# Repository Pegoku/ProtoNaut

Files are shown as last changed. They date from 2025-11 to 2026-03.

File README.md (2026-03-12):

# ProtoNaut

ProtoNaut is a custom-designed 3D printer. Built using 2020 aluminum extrusions, linear rails, and NEMA 17 stepper motors, this printer aims to deliver reliable performance in a compact cantilever design while maintaining a budget-ish build cost of approximately $400.

The project utilizes Klipper for motion control, running on an Orange Pi Zero 3 with a BIGTREETECH SKR PICO controller. The design tries to achieve precision, ease of assembly, and fully open-source design through FreeCAD CAD files.

## Images

BUILD

<details>
<summary>CAD - click to expand</summary>

ProtoNaut CAD

</details>

## Features

- Cantilever Design
- Magnetic PEI Bed
- Automatic Bed Leveling using the BTT EDDY  
- Klipper firmware
- 150x150mm Build Volume

## BOM (Bill of Materials)
[ONLINE GOOGLE SHEETS](https://docs.google.com/spreadsheets/d/10S4NtRr_S8fiZ1eurKxR3v34cEba0Mtye6buwyMkIno/edit?usp=sharing)

| Item | Qtty | 4.19€  | Source | Extra | Category | Item Total | Final Total | Final Total ($) |
| --- | ---- | --- | --- | --- | --- | --- | --- | --- |
| Bed Spring Leveling kit | 1 | 5.19€  | https://es.aliexpress.com/item/1005003097384079.html  | Black(M3) 1Set | Bed | 5.19€ | 346.64€ | $398.13 |
| Bed support Y axis | 1 | 10.49€ | https://es.aliexpress.com/item/1005005526138056.html  | | Bed | 10.49€ | | |
| 12V 80W heatbed 150x150 | 1 | 8.59€  | https://es.aliexpress.com/item/1005001417127602.html  | | Bed | 8.59€ | | |
| Magnetic Sticker | 1 | 5.09€  | https://es.aliexpress.com/item/1005007297499038.html  | | Bed | 5.09€ | | |
| Orange Pi Zero 3 | 1 | 21.11€ | https://es.aliexpress.com/item/1005005785695181.html  | Bundle 3, 1GB RAM | Electronics | 21.11€ | | |
| BIGTREETECH SKR PICO | 1 | 22.39€ | https://es.aliexpress.com/item/1005009051136182.html  | | Electronics | 22.39€ | | |
| 12V PSU | 1 | 18.99€ | https://es.aliexpress.com/item/1005007287646072.html  | LRS-100-12 | Electronics | 18.99€ | | |
| 24V PSU | 1 | 33.59€ | https://es.aliexpress.com/item/1005007234003604.html  | LRS-200, 24V | Electronics | 33.59€ | | |
| PSU terminals | 1 | 2.95€  | https://www.aliexpress.com/item/1005007254348481.html | | Electronics | 2.95€ | | |
| HGX Lite | 1 | 19.19€ | https://es.aliexpress.com/item/1005006950563760.html  | Red add Motor | Extruder | 19.19€ | | |
| TZ E3 2.0 Hotend | 1 | 14.89€ | https://es.aliexpress.com/item/1005008453023317.html  | Hotend -- B2468 | Extruder | 14.89€ | | |
| BIGTREETECH EDDY | 1 | 20.59€ | https://es.aliexpress.com/item/1005006917784069.html  | | Extruder | 20.59€ | | |
| 4010 blower | 1 | 3.19€  | https://es.aliexpress.com/item/1005009427457896.html  | 4010 24V 2P2.54 | Extruder | 3.19€ | | |
| 3010 fan | 3 | 1.70€  | https://es.aliexpress.com/item/1005001303394448.html  | 3010 24v | Extruder, Electronics | 5.10€ | | |
| Idler 20T W6 B3 | 1 | 4.19€  | https://es.aliexpress.com/item/1005009619469013.html  | 20T W6 B3 With T | Linear | 4.19€ | | |
| Idler 16T W6 B3 | 1 | 4.19€  | https://es.aliexpress.com/item/1005009619469013.html  | 16T W6 B3 With T | Linear | 4.19€ | | |
| Idler 20T W6 B5 | 1 | 4.19€  | https://es.aliexpress.com/item/1005009619469013.html  | 20T W6 B5 With T | Linear | 4.19€ | | |
| belt 6mm | 1 | 4.29€  | https://es.aliexpress.com/item/1005004822740666.html  | 6MM 2GT, 2 meters | Linear | 4.29€ | | |
| Pulley 20T W6 B5 | 2 | 1.14€  | https://es.aliexpress.com/item/1005009023224783.html  | 20T W6 B5 | Linear | 2.27€ | | |
| Nema 17 stepper | 3 | 7.69€  | https://es.aliexpress.com/item/1005008459399126.html  | | Motor | 23.07€ | | |
| 5mm Pin | 1 | 4.49€  | https://es.aliexpress.com/item/4000473863693.html | 25mm | screws | 4.49€ | | |
| m6 10642 screw | 1 | 2.65€  | https://es.aliexpress.com/item/32934186482.html | M6, 30mm | screws | 2.65€ | | |
| m6 4762 screw | 1 | 3.39€  | https://es.aliexpress.com/item/1005006999030038.html  | M6, 30mm, DIN912 | screws | 3.39€ | | |
| m5 10642 screw | 1 | 1.44€  | https://es.aliexpress.com/item/32934186482.html | M5, 8mm | screws | 1.44€ | | |
| m3 10642 screw | 1 | 3.59€  | https://es.aliexpress.com/item/32934186482.html | M3, 40mm | screws | 3.59€ | | |
| m3 4762 screw | 1 | 2.99€  | https://es.aliexpress.com/item/1005006999030038.html  | M3, 8 mm, DIN912 | screws | 2.99€ | | |
| m3 4762 screw | 1 | 2.76€  | https://es.aliexpress.com/item/1005006999030038.html  | M3, 6 mm, DIN912 | screws | 2.76€ | | |
| m3 4762 screw | 1 | 3.09€  | https://es.aliexpress.com/item/1005006999030038.html  | M3, 14 mm, DIN912 | screws | 3.09€ | | |
| m3 4762 screw | 1 | 3.19€  | https://es.aliexpress.com/item/1005006999030038.html  | M3, 16 mm, DIN912 | screws | 3.19€ | | |
| m3 4762 screw | 1 | 3.29€  | https://es.aliexpress.com/item/1005006999030038.html  | M3, 20 mm, DIN912 | screws | 3.29€ | | |
| M5 T-nut | 1 | 3.39€  | https://es.aliexpress.com/item/1005008147125860.html  | 20-M3 | screws | 3.39€ | | |
| M3 T-nut | 1 | 3.29€  | https://es.aliexpress.com/item/1005008147125860.html  | 20-M5 | screws | 3.29€ | | |
| M6 Tap | 1 | 4.59€  | https://es.aliexpress.com/item/32788074995.html | | screws | 4.59€ | | |
| 3mm Pin | 1 | 3.29€  | https://es.aliexpress.com/item/4000473863693.html | 30 mm | screws | 3.29€ | | |
| heatset inserts | 1 | 3.39€  | https://es.aliexpress.com/item/1005007973137842.html  | M3x5x4 | screws | 3.39€ | | |
| 2020 extrusion | 1 | 2.65€  | https://es.aliexpress.com/item/1005003299342998.html  | 130mm | Structure | 2.65€ | | |
| 2020 bracket corner | 1 | 6.19€  | https://es.aliexpress.com/item/1005005748992965.html  | | Structure | 6.19€ | | |
| MGN9C rail | 1 | 9.79€  | https://es.aliexpress.com/item/1005009577277063.html  | 200 mm | X axis | 9.79€ | | |
| 2020 extrusion | 1 | 4.09€  | https://es.aliexpress.com/item/1005003299342998.html  | 250 mm | X axis, Y axis, Structure | 4.09€ | | |
| 2020 extrusion | 1 | 6.69€  | https://es.aliexpress.com/item/1005009577277063.html  | 250 mm | X axis, Y axis, Structure | 6.69€ | | |
| MGN12c rail | 2 | 10.69€ | https://es.aliexpress.com/item/1005009577277063.html  | 200 mm | Y axis, Z axis | 21.38€ | | |
| 5x8 coupler | 1 | 3.59€  | https://es.aliexpress.com/item/1005006305848755.html  | 5x8 | Z axis | 3.59€ | | |
| T8 lead screw | 1 | 5.29€  | https://es.aliexpress.com/item/1005003312523975.html  | 250 mm, Pitch 2mm Lead 8mm | Z axis, Linear | 5.29€ | | |
| 2020 extrusion | 1 | 4.59€  | https://es.aliexpress.com/item/1005003299342998.html  | 280 mm | Z axis, Structure | 4.59€ | | |

**Estimated Total Cost**: €344.04 (~$396.46 USD)

## Design Specifications

- **Build Volume**: 150mm x 150mm
- **Bed Type**: Heated magnetic adhesion surface
- **Motion System**: Linear rail guided on all axes
- **Nozzle Type**: 0.4mm standard
- **Control Board**: BIGTREETECH SKR PICO
- **Host Controller**: Orange Pi Zero 3 (1GB RAM)
- **Firmware**: Klipper with Mainsail/Fluidd interface

## Wiring Diagram

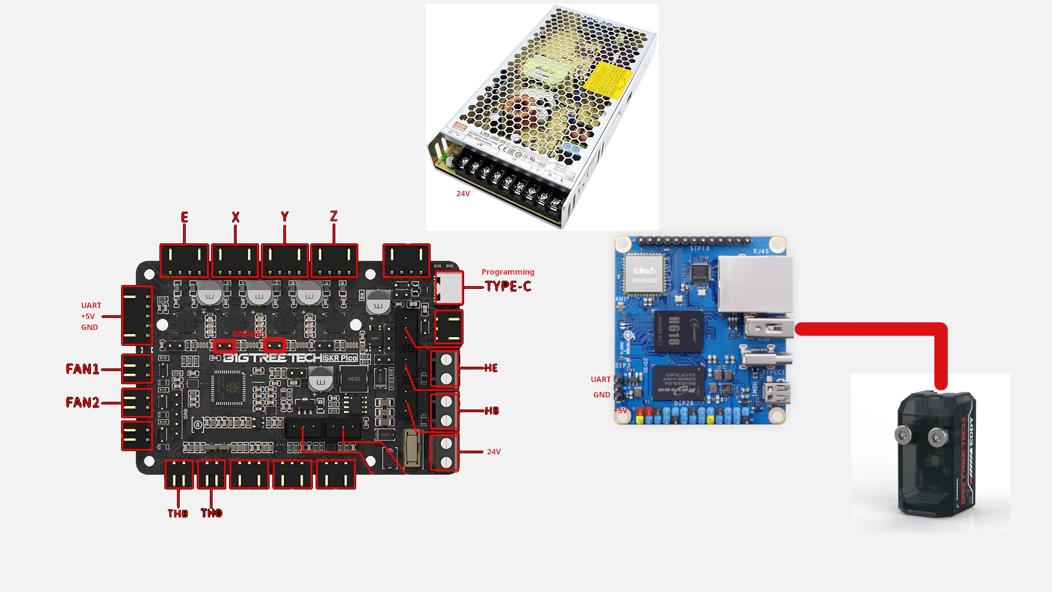
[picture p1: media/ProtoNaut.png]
wiring


## License

This work is licensed under a
[Creative Commons Attribution-NonCommercial 4.0 International License][cc-by-nc].

[][cc-by-nc]

[cc-by-nc]: https://creativecommons.org/licenses/by-nc/4.0/
[cc-by-nc-image]: https://licensebuttons.net/l/by-nc/4.0/88x31.png
[cc-by-nc-shield]: https://img.shields.io/badge/License-CC%20BY--NC%204.0-lightgrey.svg

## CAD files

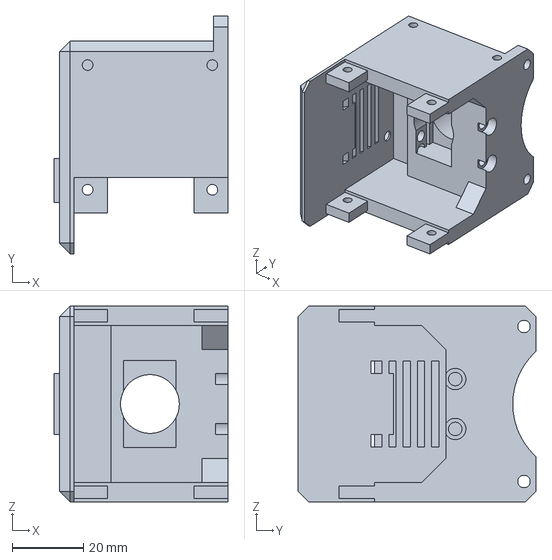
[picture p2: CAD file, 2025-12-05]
CAD/Printed Parts/Printer-zAxisToolheadCase.step
48.7 x 66.8 x 55.0 mm

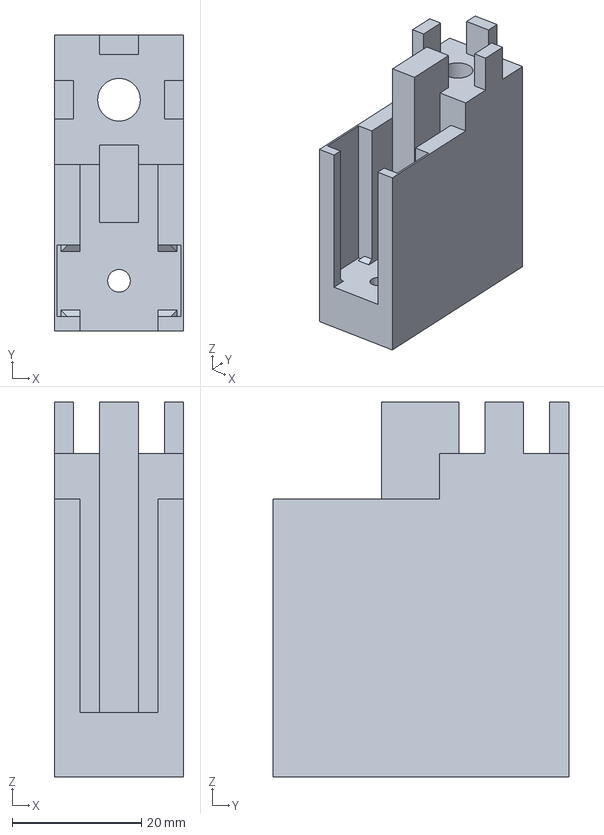
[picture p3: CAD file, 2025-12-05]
CAD/Printed Parts/Printer-zAxisSupport.step
20.0 x 45.8 x 58.0 mm

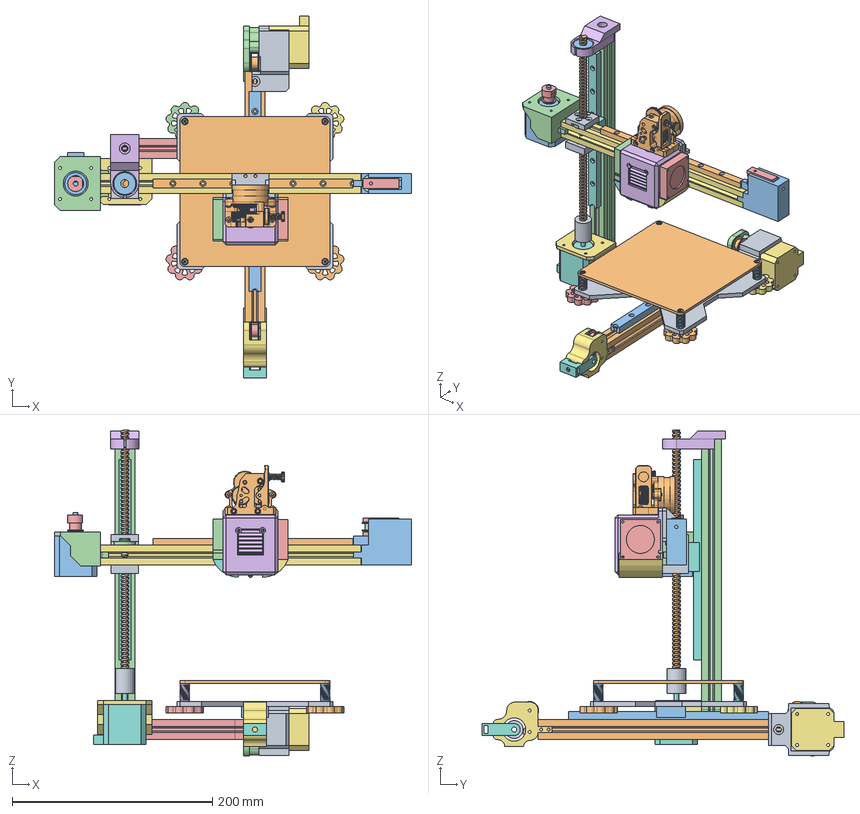
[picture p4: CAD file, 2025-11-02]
CAD/Printer.FCStd
356.4 x 361.2 x 325.4 mm
Bed support
150x150Bed
M3x30-Screw
LevelNut
Spring
M3x30-Screw004
LevelNut001
Spring001
M3x30-Screw005
LevelNut002
Spring002
M3x30-Screw006
LevelNut003
Spring003
17HS4401 1
Pulley 20T W6 B5 1
Bottom Motor mount
Idler 20T W6 B3 1
Idler 16T W6 B3 1
Top Motor Mount
Idler 20T W6 B3 002
Idler 16T W6 B3 002
TensionerA
TensionerB
Idler 20T W6 B5 1
MGN12C001
BearingHolder
zMotorHolder
17HS44012
Coupling 5x8
T8 Lead
608ZZ
T8 Nut
M5x8-Screw
M5x8-Screw001
xAxis2020
MGN12C
2020Support
MGN9
17HS44014
xMotorHolder
Pulley 20T W6 B5 3
Collet-V6
M1.6 Titanium Alloy Screw B (1)
Nozzle (1)
Heater (1)
Clamp (1)
Heatbreak (1)
HeatBlock (1)
Sock (1)
M3 Setscrew (1)
M1.6 Titanium Alloy Screw B (2)
M3 Setscrew (2)
LGX\X2\91D15C5E632451FA 673A\X0\
3010 fan
4010 blower 1
4010 blower 2
ToolheadCase
ToolheadAirDuct
ToolheadAirDuct001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

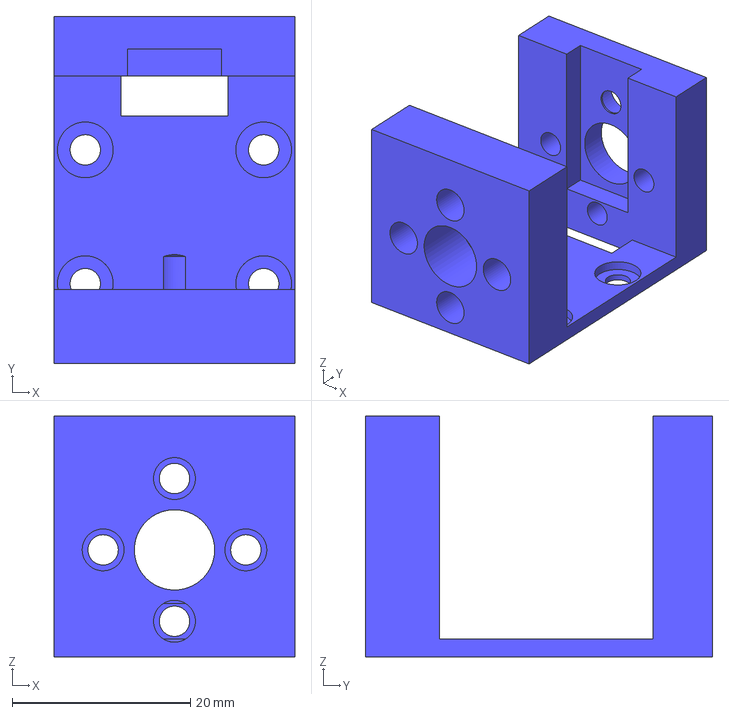
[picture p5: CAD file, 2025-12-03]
CAD/Printed Parts/Printer-zAxis2020Support.step
27.0 x 38.9 x 27.0 mm

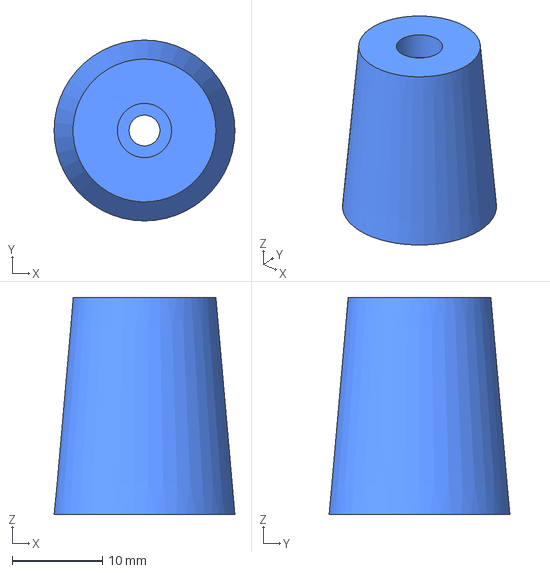
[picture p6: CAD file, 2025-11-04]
CAD/Printed Parts/Printer-PrinterFeet001RubberFeet001.step
20.0 x 20.0 x 24.0 mm

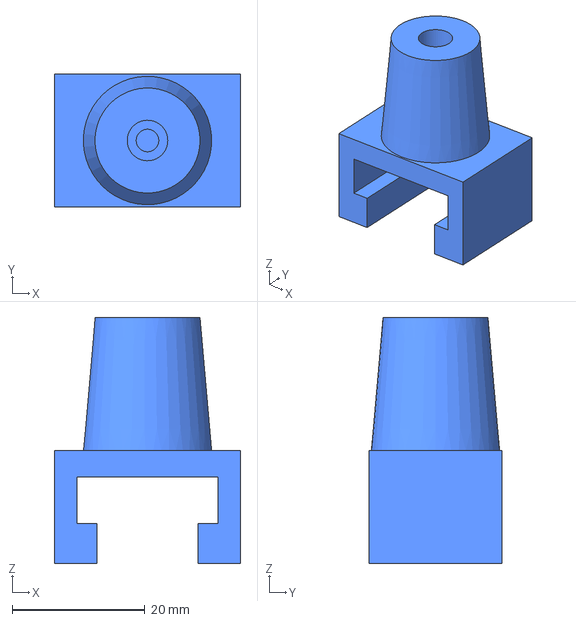
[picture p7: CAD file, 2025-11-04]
CAD/Printed Parts/Printer-PrinterFeetRubberFeet.step
28.0 x 20.0 x 37.0 mm

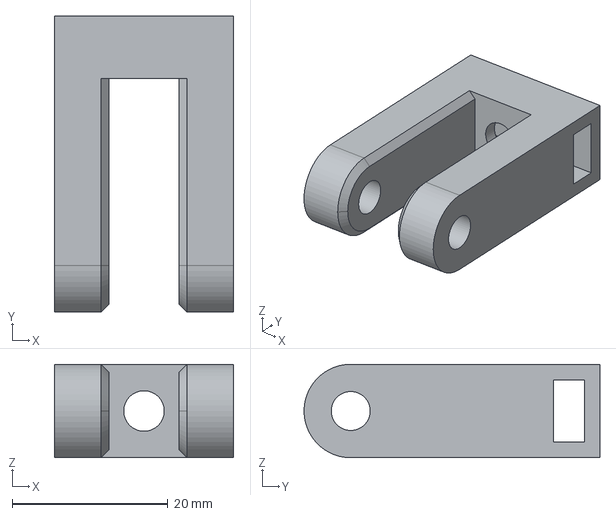
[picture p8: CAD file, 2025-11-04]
CAD/Printed Parts/Printer-yAxisTensionerB.step
23.0 x 38.0 x 12.0 mm

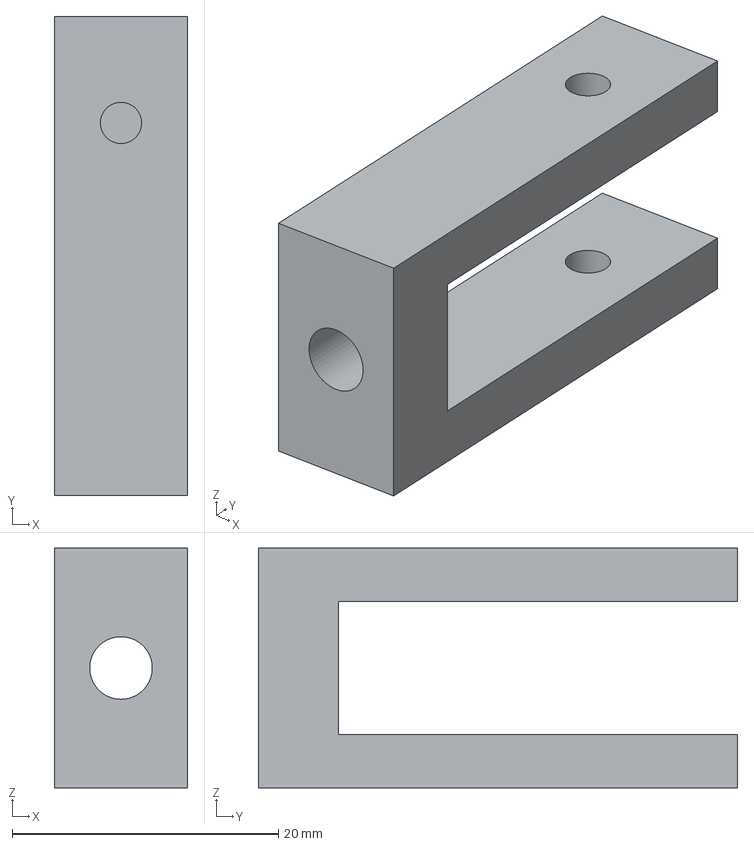
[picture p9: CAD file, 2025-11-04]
CAD/Printed Parts/Printer-zAxisTensioner.step
10.0 x 36.0 x 18.0 mm

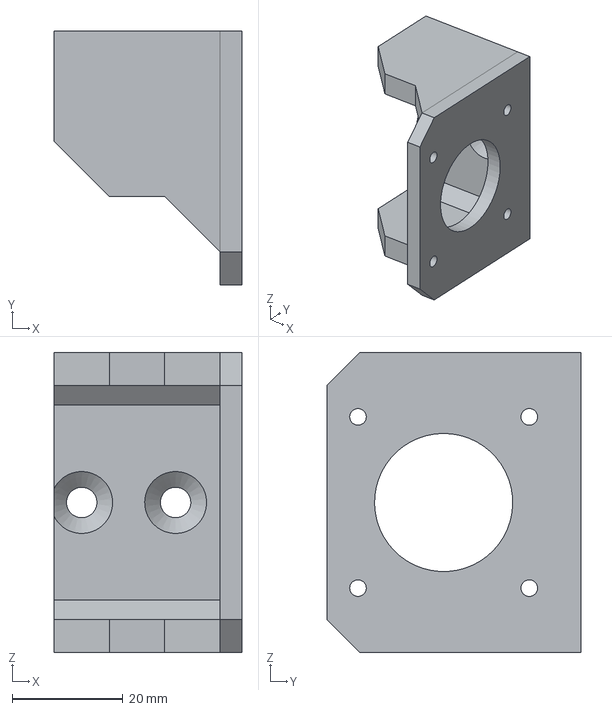
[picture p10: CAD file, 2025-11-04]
CAD/Printed Parts/Printer-zAxiszMotorHolder.step
34.0 x 46.1 x 54.3 mm

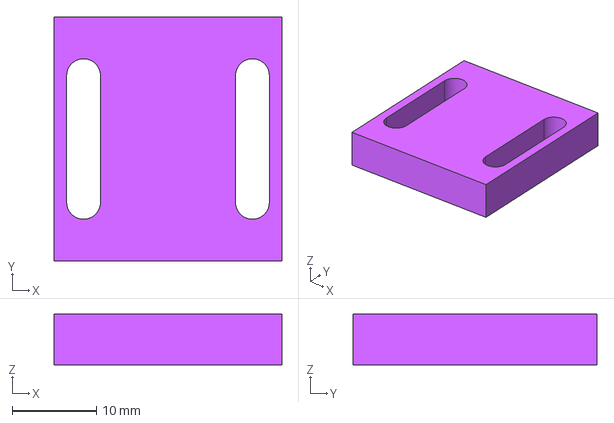
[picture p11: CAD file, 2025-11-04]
CAD/Printed Parts/Printer-yAxisBed spacer.step
27.0 x 28.9 x 6.00 mm

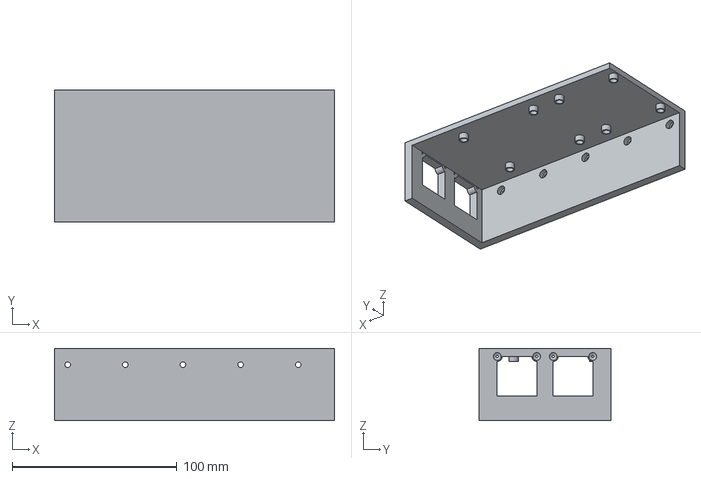
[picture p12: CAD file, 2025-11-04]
CAD/Printed Parts/Printer-ElectronicsElectronicsCase.step
170.0 x 80.0 x 44.0 mm

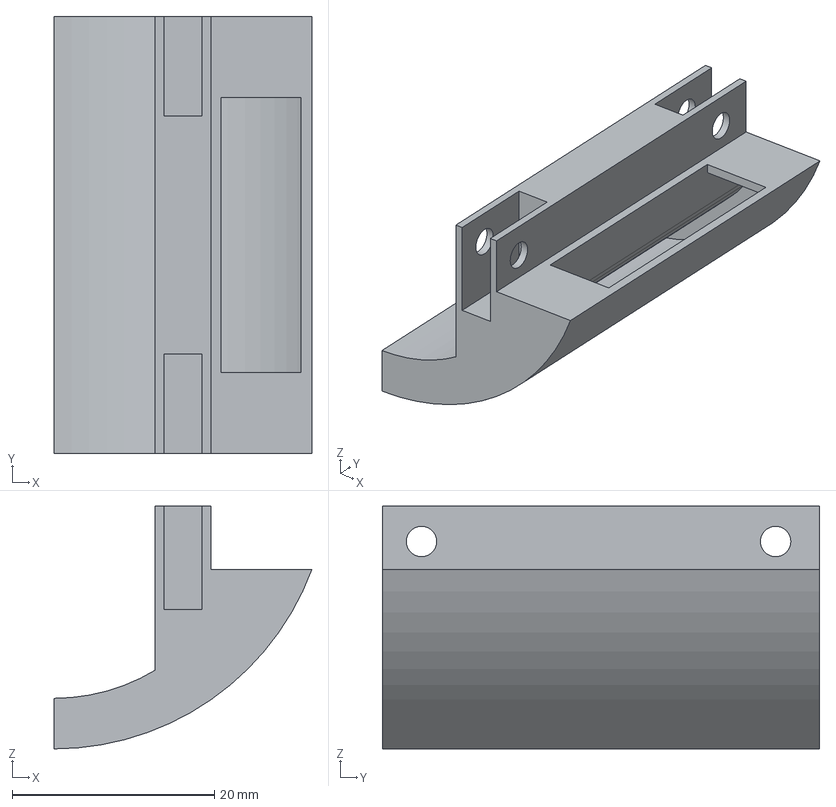
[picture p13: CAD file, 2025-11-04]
CAD/Printed Parts/Printer-zAxisToolheadAirDuct.step
25.5 x 43.2 x 24.0 mm

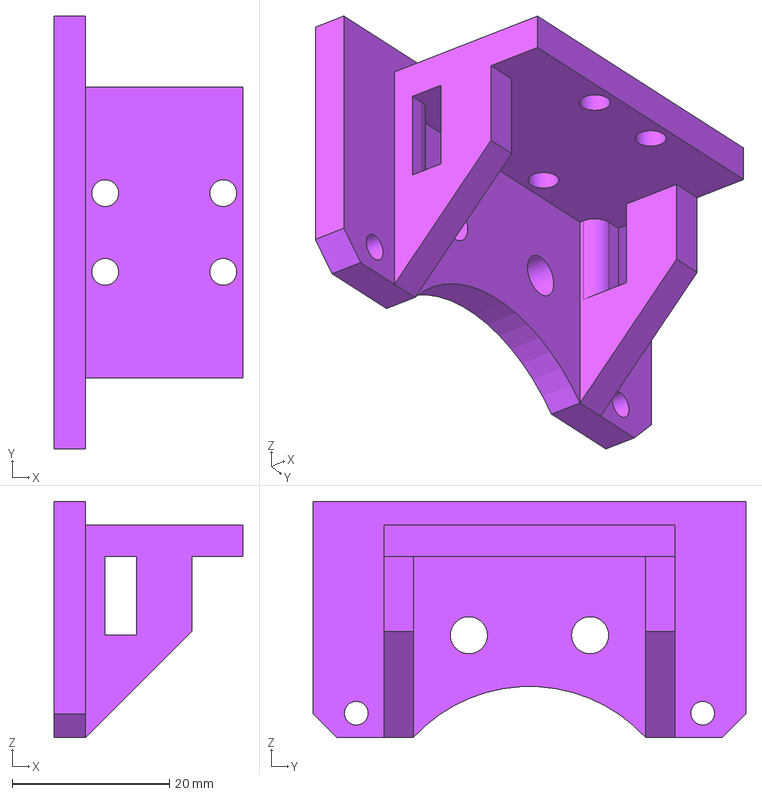
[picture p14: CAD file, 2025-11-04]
CAD/Printed Parts/Printer-zAxisToolheadSupport.step
24.0 x 55.0 x 30.0 mm

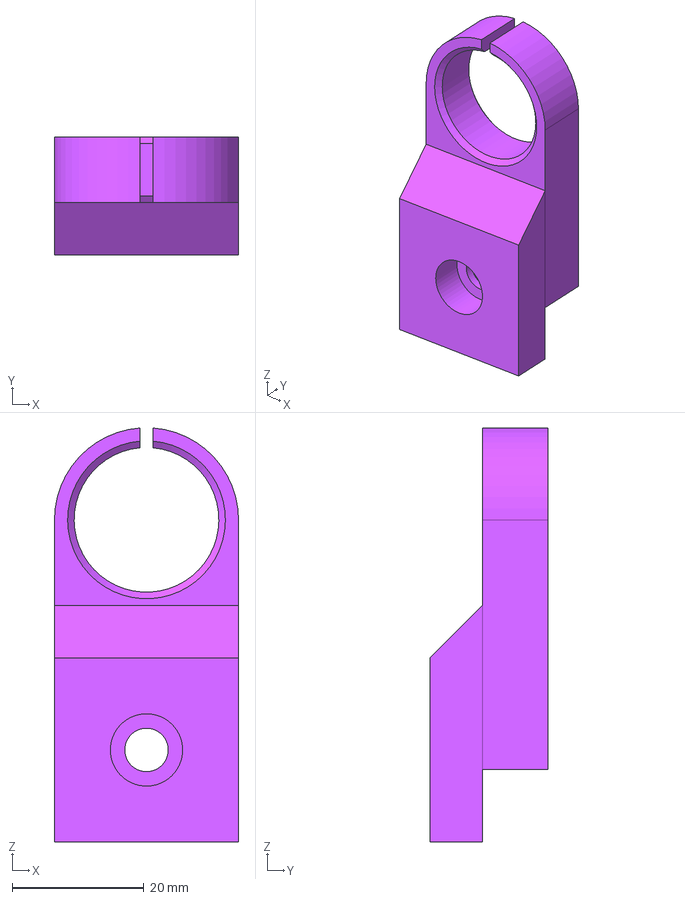
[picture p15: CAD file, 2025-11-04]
CAD/Printed Parts/Printer-zAxisBearingHolder.step
28.0 x 18.0 x 63.0 mm

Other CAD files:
CAD/Assembly.step
CAD/Printed Parts/Printer-zAxisToolheadAirDuct2.step
CAD/Printed Parts/Printer-zAxisBeltClamp.step
CAD/Printed Parts/Printer-yAxisTensionerA.step
CAD/Printed Parts/Printer-yAxisBottom Motor mount.step
CAD/Printed Parts/Printer-yAxisTop Motor Mount.step
CAD/Printed Parts/Printer-zAxisxMotorHolder.step

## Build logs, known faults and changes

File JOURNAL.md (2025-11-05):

<!--
  ===================    !!READ THIS NOTICE!!   ====================
  DO NOT edit this file manually. Your changes WILL BE OVERWRITTEN!
  This journal is auto generated and updated by Hack Club Blueprint.
  To edit this file, please edit your journal entries on Blueprint.
  ==================================================================
-->

## 10/18/2025 - Start the planning of the 3d printer  

This printer is the first one I've ever designed.
I would like this printer to be cantilever, small, use klipper, and be relatively cheap (-200$ if possible).
I've been thinking of going with 2020 aluminum extrusions, Nema 17 motors, Voron V0 bed, and linear rails 12 and 9 mm.

Sketch I did:


## 10/20/2025 - Change of plans  

I changed plans, and I think I will no longer go with a voron V0 bed. Mainly due to the hard mounting options, and also, the hard leveling. This is why I will go with a 150x150mm bed.
After quite a bit of research, I've found many parts which seem to fit the printer.
This is the current BOM:



## 10/22/2025 - Learn CFDOF with freecad  

Today I wanted to learn what was CFD and how to use, as I think this is going to be a necessary tool for my toolhead design. I wanted to use it with FreeCAD (the CAD software I use).
After quite a LOT of trial and error, I was able to get a basic simulation working.

I still have a lot to learn, but this is a good start





## 10/24/2025 - Do HotBed and create models  

I have been creating and importing models for my 3Dp. I've imported the extruder, hotend and SKR PICO.
I've also designed the bed and Y axis. I have yet to decide the dimensions of the Y axis, as well as the X and Z. I'll probably just design them, and then, later, resize them to the correct dimensions.



## 10/29/2025 6 PM - Finish bed motor mount, belt tensioner and start toolhead  

I just finished my completely overengineered motor mount and belt system.
It will use a NEMA 17 stepper motor (same motor will be used for all the other axis), and 2 pulleys to guide the belt through the correct paths.
I know there are WAY easier ways to route that, but I went too deep into the "cool" design.

I will now be designing the toolhead. Hope it works!



## 10/29/2025 7 PM - Finish toolhead  

I just finished the toolhead for my printer. It will use a 3010 fan to cool the heatsink, and 2x 4010 blower fans to cool the nozzle.
It will be powered by the [TZ E3 2.0 Hotend](https://es.aliexpress.com/item/1005008453023317.html), and [HGX Lite extruder](https://es.aliexpress.com/item/1005006950563760.html).



## 11/1/2025 - Start Z axis  

Now I've been working on the Z axis of the printer. I will be using a T8 lead screw for the axis, and will secure it to the T8 nut. I will be adding a linear rail, probably an MGN12C, and then continue with the X axis. 
I'm getting so close! 





## 11/3/2025 10 AM - Finish base printer  

I finished the base printer, and that means I'm near the finish line!
All the structure, motors, etc. Are done. I only need to add a few parts, e.g. controller, SBC, eddy, PSUs...

Current state of the printer: 




## 11/3/2025 12 PM - Finish the printer!  

I just finished the printer!
It was a long journey, but I finally did it. I can't wait to build it IRL.
I'll now do the final checks and finish the BOM. After that, I'll start ordering the pieces!





## 11/3/2025 7 PM - Finish BOM  

I redid and finished the BOM. I *hope* I got everything right. I probably could have designed it better so it used fewer components (or cheaper ones), but I didn't want to compromise the build. That's why I used linear rails, good motors, etc.

Made a [Google Sheets](https://docs.google.com/spreadsheets/d/10S4NtRr_S8fiZ1eurKxR3v34cEba0Mtye6buwyMkIno/edit?usp=sharing) with the [BOM](https://docs.google.com/spreadsheets/d/10S4NtRr_S8fiZ1eurKxR3v34cEba0Mtye6buwyMkIno/edit?usp=sharing) 



## 11/4/2025 9 AM - Export printed files  

I exported all the printed parts from the FreeCAD file. They should be all the [files](https://github.com/Pegoku/ProtoNaut/tree/main/CAD/Printed%20Parts).



## 11/4/2025 8 PM - Add Assembly.step  

I added the [Assembly.step](https://github.com/Pegoku/ProtoNaut/blob/main/CAD/Assembly.step) file. I had to use Git LFS because the file was 102MB (100MB max) :sob:



## 11/5/2025 - Add colors to the design, and use 2040 extrusion for Z axis  

Thanks to the help of the reviewers, I was able to fix one of my design errors, using a single 2020 extrusion for the Z axis. So to fix it, I used a 2040 instead. 
Sadly, I already bought the components and can't cancel them.
While at it, I also added colors to the printer. I chose red and black for the main parts.



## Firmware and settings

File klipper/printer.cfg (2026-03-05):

[include fluidd.cfg]

[mcu]
serial: /dev/serial/by-id/usb-Klipper_rp2040_5044506110E0521C-if00

[mcu eddy]
serial: /dev/serial/by-id/usb-Klipper_rp2040_5044506130870F1C-if00
restart_method: command

[printer]
kinematics: cartesian
max_velocity: 150
max_accel: 1500
max_z_velocity: 3
max_z_accel: 60

[force_move]
enable_force_move: true

[gcode_macro UNSAFE_ALLOW_JOG]
description: Allow Fluidd jogging without homing
gcode:
  SET_KINEMATIC_POSITION X=0 Y=0 Z=0

[gcode_macro UNSAFE_CLEAR_KINEMATIC]
description: Clear fake kinematic position
gcode:
  SET_KINEMATIC_POSITION CLEAR=XYZ

[stepper_x]
step_pin: gpio11
dir_pin: !gpio10
enable_pin: !gpio12
microsteps: 16
rotation_distance: 40
endstop_pin: tmc2209_stepper_x:virtual_endstop
position_endstop: 0
position_max: 235
homing_speed: 40
homing_retract_dist: 0

[tmc2209 stepper_x]
uart_pin: gpio9
tx_pin: gpio8
uart_address: 0
diag_pin: ^gpio4
run_current: 0.580
stealthchop_threshold: 0
driver_SGTHRS: 80

[stepper_y]
step_pin: gpio6
dir_pin: !gpio5
enable_pin: !gpio7
microsteps: 16
rotation_distance: 40
endstop_pin: tmc2209_stepper_y:virtual_endstop
position_endstop: -70
position_min: -70
position_max: 85
homing_speed: 40
homing_retract_dist: 0

[tmc2209 stepper_y]
uart_pin: gpio9
tx_pin: gpio8
uart_address: 2
diag_pin: ^gpio3
run_current: 0.580
stealthchop_threshold: 0
driver_SGTHRS: 80

[stepper_z]
step_pin: gpio19
dir_pin: !gpio28
enable_pin: !gpio2
microsteps: 16
rotation_distance: 8
endstop_pin: probe:z_virtual_endstop
position_max: 250

[tmc2209 stepper_z]
uart_pin: gpio9
tx_pin: gpio8
uart_address: 1
run_current: 0.580
stealthchop_threshold: 999999

[extruder]
step_pin: gpio14
dir_pin: !gpio13
enable_pin: !gpio15
microsteps: 16
rotation_distance: 33.500
nozzle_diameter: 0.400
filament_diameter: 1.750
heater_pin: gpio23
sensor_type: EPCOS 100K B57560G104F
sensor_pin: gpio27
control: pid
pid_Kp: 21.527
pid_Ki: 1.063
pid_Kd: 108.982
min_temp: 0
max_temp: 250

[tmc2209 extruder]
uart_pin: gpio9
tx_pin: gpio8
uart_address: 3
run_current: 0.650
stealthchop_threshold: 999999

[heater_bed]
heater_pin: gpio21
sensor_type: ATC Semitec 104GT-2
sensor_pin: gpio26
control: pid
pid_Kp: 54.027
pid_Ki: 0.770
pid_Kd: 948.182
min_temp: 0
max_temp: 130

[fan]
pin: gpio17

[heater_fan heatbreak_cooling_fan]
pin: gpio18

[heater_fan controller_fan]
pin: gpio20

[temperature_sensor pico]
sensor_type: temperature_mcu

[temperature_sensor eddy_mcu]
sensor_type: temperature_mcu
sensor_mcu: eddy

[probe_eddy_current btt_eddy]
sensor_type: ldc1612
z_offset: 2.5
i2c_mcu: eddy
i2c_bus: i2c0f
x_offset: 0
y_offset: -36

[temperature_probe btt_eddy]
sensor_type: Generic 3950
sensor_pin: eddy:gpio26
horizontal_move_z: 1

[bed_mesh]
horizontal_move_z: 1
speed: 80
mesh_min: 5, 5
mesh_max: 125, 44
probe_count: 9, 9
algorithm: bicubic

[safe_z_home]
home_xy_position: 75, 60
z_hop: 10
z_hop_speed: 25
speed: 200

[bed_screws]
screw1: 20, 10
screw1_name: front_left
screw2: 130, 10
screw2_name: front_right
screw3: 130, 40
screw3_name: rear_right
screw4: 20, 40
screw4_name: rear_left
horizontal_move_z: 5
speed: 80

[gcode_macro G28]
rename_existing: G28.1
gcode:
  G28.1 {rawparams}
  {% if not rawparams or (rawparams and 'Z' in rawparams) %}
    PROBE
    SET_Z_FROM_PROBE
  {% endif %}

[gcode_macro SET_Z_FROM_PROBE]
gcode:
  {% set cf = printer.configfile.settings %}
  SET_GCODE_OFFSET_ORIG Z={printer.probe.last_z_result - cf['probe_eddy_current btt_eddy'].z_offset + printer["gcode_macro SET_GCODE_OFFSET"].runtime_offset}
  G90
  G1 Z{cf.safe_z_home.z_hop}

[gcode_macro SET_GCODE_OFFSET]
rename_existing: SET_GCODE_OFFSET_ORIG
variable_restored: False
variable_runtime_offset: 0
gcode:
  SET_GCODE_OFFSET_ORIG { rawparams }

[gcode_macro PROBE_EDDY_CURRENT_CALIBRATE_AUTO]
gcode:
  BED_MESH_CLEAR
  G28 X Y
  G90
  G1 X{ (printer.toolhead.axis_minimum.x + printer.toolhead.axis_maximum.x) / 2 } Y{ (printer.toolhead.axis_minimum.y + printer.toolhead.axis_maximum.y) / 2 } F6000
  {% if 'z' not in printer.toolhead.homed_axes %}
    SET_KINEMATIC_POSITION Z={ printer.toolhead.axis_maximum.z-1 }
  {% endif %}
  PROBE_EDDY_CURRENT_CALIBRATE {rawparams}

[gcode_macro SINE_ALL_AXES]
description: Move XYZ in a synchronized sine-like path
gcode:
  {% set cycles = params.CYCLES|default(2)|int %}
  {% set feed = params.F|default(6000)|int %}
  {% if 'x' not in printer.toolhead.homed_axes or 'y' not in printer.toolhead.homed_axes or 'z' not in printer.toolhead.homed_axes %}
    {action_raise_error("Home XYZ first (G28) before SINE_ALL_AXES")}
  {% endif %}

  {% set xmin = printer.toolhead.axis_minimum.x + 10.0 %}
  {% set xmax = printer.toolhead.axis_maximum.x - 10.0 %}
  {% set ymin = printer.toolhead.axis_minimum.y + 10.0 %}
  {% set ymax = printer.toolhead.axis_maximum.y - 10.0 %}
  {% set zmin = 8.0 %}
  {% set zmax = [printer.toolhead.axis_maximum.z - 20.0, 35.0]|min %}
  {% if zmax <= zmin + 2.0 %}
    {action_raise_error("Z travel too small for SINE_ALL_AXES")}
  {% endif %}

  {% set xmid = (xmin + xmax) / 2.0 %}
  {% set ymid = (ymin + ymax) / 2.0 %}
  {% set zmid = (zmin + zmax) / 2.0 %}
  {% set xamp = (xmax - xmin) / 2.0 %}
  {% set yamp = (ymax - ymin) / 2.0 %}
  {% set zamp = (zmax - zmin) / 2.0 %}

  {% set sx = [0.0, 0.3827, 0.7071, 0.9239, 1.0, 0.9239, 0.7071, 0.3827, 0.0, -0.3827, -0.7071, -0.9239, -1.0, -0.9239, -0.7071, -0.3827] %}
  {% set sy = [1.0, 0.9239, 0.7071, 0.3827, 0.0, -0.3827, -0.7071, -0.9239, -1.0, -0.9239, -0.7071, -0.3827, 0.0, 0.3827, 0.7071, 0.9239] %}
  {% set sz = [0.7071, 0.9239, 1.0, 0.9239, 0.7071, 0.3827, 0.0, -0.3827, -0.7071, -0.9239, -1.0, -0.9239, -0.7071, -0.3827, 0.0, 0.3827] %}

  G90
  G1 X{xmid} Y{ymid} Z{zmin + 2.0} F{feed}
  {% for _ in range(cycles) %}
    {% for i in range(16) %}
      {% set xx = xmid + xamp * sx[i] %}
      {% set yy = ymid + yamp * sy[i] %}
      {% set zz = zmid + zamp * sz[i] %}
      G1 X{xx} Y{yy} Z{zz} F{feed}
    {% endfor %}
  {% endfor %}
  G1 X{xmid} Y{ymid} Z{zmin + 2.0} F{feed}

[virtual_sdcard]
path: /home/pegoku/printer_data/gcodes
on_error_gcode: CANCEL_PRINT

#*# <---------------------- SAVE_CONFIG ---------------------->
#*# DO NOT EDIT THIS BLOCK OR BELOW. The contents are auto-generated.
#*#
#*# [probe_eddy_current btt_eddy]
#*# reg_drive_current = 15
#*# calibrate =
#*# 	0.050000:3234334.275,0.090000:3233995.129,0.130000:3233592.364,
#*# 	0.170000:3233304.346,0.210000:3232967.287,0.250000:3232622.251,
#*# 	0.290000:3232301.665,0.330000:3231964.034,0.370000:3231654.382,
#*# 	0.410000:3231341.157,0.450000:3231065.800,0.490000:3230770.367,
#*# 	0.530000:3230446.119,0.570000:3230150.199,0.610000:3229865.124,
#*# 	0.650000:3229578.082,0.690000:3229297.957,0.730000:3229032.796,
#*# 	0.770000:3228760.740,0.810000:3228529.876,0.850000:3228279.518,
#*# 	0.890000:3228021.851,0.930000:3227792.569,0.970000:3227502.081,
#*# 	1.010000:3227256.623,1.050000:3227012.281,1.090000:3226809.554,
#*# 	1.130000:3226573.566,1.170000:3226331.325,1.210000:3226124.123,
#*# 	1.250000:3225907.406,1.290000:3225691.481,1.330000:3225453.592,
#*# 	1.370000:3225219.775,1.410000:3225015.280,1.450000:3224789.075,
#*# 	1.490000:3224584.973,1.530000:3224369.913,1.570000:3224155.249,
#*# 	1.610000:3223936.984,1.650000:3223762.867,1.690000:3223568.532,
#*# 	1.730000:3223385.224,1.770000:3223210.507,1.810000:3223013.678,
#*# 	1.850000:3222850.338,1.890000:3222666.804,1.930000:3222502.654,
#*# 	1.970000:3222322.653,2.010000:3222163.271,2.050000:3221957.050,
#*# 	2.090000:3221801.405,2.130000:3221652.508,2.170000:3221490.236,
#*# 	2.210000:3221318.437,2.250000:3221184.954,2.290000:3221051.181,
#*# 	2.330000:3220868.878,2.370000:3220737.997,2.410000:3220596.978,
#*# 	2.450000:3220461.293,2.490000:3220320.632,2.530000:3220157.889,
#*# 	2.570000:3220032.955,2.610000:3219895.651,2.650000:3219768.430,
#*# 	2.690000:3219605.693,2.730000:3219487.474,2.770000:3219358.694,
#*# 	2.810000:3219238.438,2.850000:3219107.140,2.890000:3218950.880,
#*# 	2.930000:3218844.857,2.970000:3218695.089,3.010000:3218612.062,
#*# 	3.050000:3218466.666,3.090000:3218336.025,3.130000:3218209.131,
#*# 	3.170000:3218080.128,3.210000:3217975.728,3.250000:3217862.725,
#*# 	3.290000:3217715.317,3.330000:3217635.157,3.370000:3217532.544,
#*# 	3.410000:3217425.823,3.450000:3217310.502,3.490000:3217236.405,
#*# 	3.530000:3217114.354,3.570000:3217021.818,3.610000:3216944.556,
#*# 	3.650000:3216813.832,3.690000:3216731.045,3.730000:3216621.563,
#*# 	3.770000:3216525.495,3.810000:3216430.008,3.850000:3216346.517,
#*# 	3.890000:3216243.103,3.930000:3216165.850,3.970000:3216070.101,
#*# 	4.010000:3215990.407,4.050000:3215901.117
#*#
#*# [temperature_probe btt_eddy]
#*# calibration_temp = 37.456327

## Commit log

2025-10-20 start BOM and CAD
    [BOM.csv, Printer.FCStd]
2025-10-22 learn CFDOF with FreeCAD
    [Printer.FCStd]
2025-10-24 Done BED
2025-10-24 continue BED
2025-10-24 Add extrusion
    [BOM.csv]
2025-10-24 add motor + pulleys
2025-10-25 finish bed motor mount
    [BOM.csv]
2025-10-27 start belt tensioner Y axis
    [BOM.csv]
2025-10-29 finish bed mount, tensioner, and start toolhead
2025-10-29 finish toolhead
2025-10-31 start z axis
2025-10-31 add axis coupling and shaft
2025-10-31 finish Z axis
2025-11-01 continue Z axis
2025-11-02 finish base printer
    [BOM.ods, Printer.FCStd]
2025-11-03 finish printer
2025-11-03 finish the printer fr
2025-11-03 fix printer
2025-11-03 add bom in ods format
    [BOM.ods]
2025-11-03 add klipper example config
    [klipper.cfg]
2025-11-04 add printed parts in .step format
    [Printer-ElectronicsElectronicsCase.step, Printer-PrinterFeet001RubberFeet001.step, Printer-PrinterFeetRubberFeet.step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]
2025-11-04 add Assembly.step
    [Assembly.step]
2025-11-05 add colors + 2040 extrusion
    [BOM.ods]
2025-12-03 update Z axis holder
    [Printer-zAxis2020Support.step]
2025-12-05 toolhead Case
    [Printer-zAxisToolheadCase.step]
2026-03-05 finish klipper
    [fluidd.cfg, printer.cfg]
2026-03-12 Wiring Diagram
